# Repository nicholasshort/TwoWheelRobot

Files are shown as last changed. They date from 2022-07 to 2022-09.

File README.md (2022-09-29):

# TwoWheelRobot

This is a project I started to learn more about control theory. 

The project consists of three main folders:
1) Arduino Code
2) Hand Derivations for the Linearized State Space Model of a Pendulum on a Cart
3) Matlab/Python Pendulum on a Cart Simulation Files

I will try to go over each folder in the remainder of this readme.

# The Robot

The Bill of Materials for this project can be found here: https://docs.google.com/document/d/1V8id3cu9YUFI_mSXT52ZumMh5tL_UX_wbOAgka5fCik/edit?usp=sharing

To control the robot, I use a PID controller, with the help of a Kalman filter (defined in KalmanFilter.h) to filter out the noise from the accelerometer and to factor in gyroscope drift. A good artilce on the fundamentals of the Kalman filter can be found here: https://blog.tkjelectronics.dk/2012/09/a-practical-approach-to-kalman-filter-and-how-to-implement-it/

One thing to note for my design was that the position of the IMU board relative to the base of the robot resulted in greater angular accelerations and thus greater noise from the accelerometer. Therefore, the measurement noise variance had to be set to a greater value than the generic value recommended in the article above. 

Here is a video of the robot maintaining balance on youtube: 

Robot (https://www.youtube.com/shorts/AJx97sAAVso)

# Hand Derivations

The two wheel robot can be modeled as a pendulum on a cart. I used Newton's Laws to derive the state space model of the pendulum-cart system, and then reduced the number of states to only focus on the angle of the pendulum.

# Matlab and Python Simulations

I used matlab and python to simulate/verify my the state space model from my hand derivations, and to develop a full-state feedback control loop to control the cart and pendulum about a fixed angle and position respectively. Running PendulumCartSim.py will show a small animation of the implementation of this control law.

Here is the animation without any control:
final_631eb3e16659cb00835e07b7_296242

Here is the animation of the linearized system with full state feedback:
final_631eb2a96fb6b5005e3506c4_549431

Additionally, I also tried to control the system using a PID controller. In "PID_Tuning.m", I implemented a very slow root-locus plot in Matlab to generate proper PID gain values to stabilize the system. An example of the root locus plot can be seen below.

Root Locus

I then used the PID values found from the locus plot to plot the system's step response (Note these are not optimal PID values)

Step Response

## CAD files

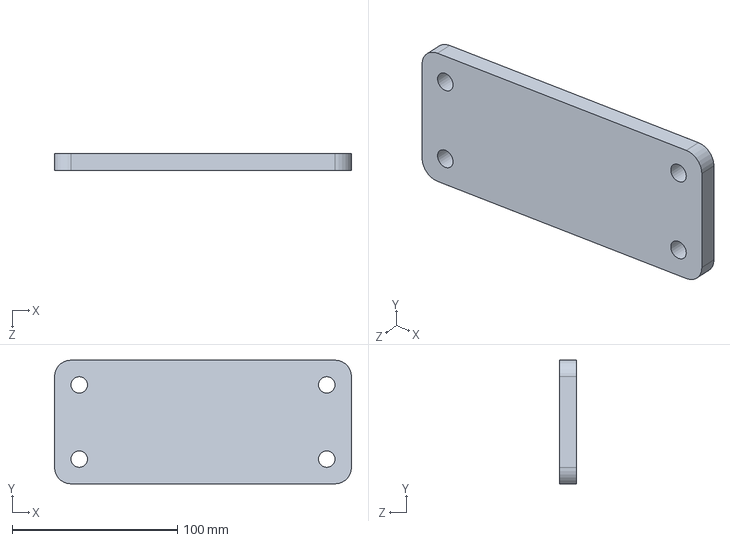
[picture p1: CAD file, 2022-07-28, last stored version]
Assembly/Platform.SLDPRT
180.0 x 75.0 x 10.0 mm

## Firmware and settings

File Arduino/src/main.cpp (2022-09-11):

#include <Arduino.h>
#include <Wire.h>
#include "KalmanFilter.h"
#include "MPU6050_Sensor.h"

#define PWM_A 6
#define PWM_B 5
#define IN_1 9
#define IN_2 7
#define IN_3 13
#define IN_4 12


MPU6050_Sensor mpu;

// Variances
float Qo = 0.001;
float Qb = 0.003;
float R = 20;

KalmanFilter kalmanFilter(Qo, Qb, R);

// Timers
unsigned long timer = 0;
float timeStep = 0.01;

// State
float* state = (float*)calloc(2, sizeof(float));

// Error variables
float error = 0;
float prevError = 0;
float totalError = 0;

// Angle
float desiredAngle = 0;

// PID Values
float Kp = 500;
float Ki = 15;
float Kd = 700;

// Controller Output
float output = 0;

// Start state variable
bool start = false;

void setup() 
{
  Serial.begin(115200);

  Serial.println("Starting...");

  state[0] = -85;

  mpu.begin();

  // Initialize pinout
  pinMode(PWM_A, OUTPUT);
  pinMode(PWM_B, OUTPUT);
  pinMode(IN_1, OUTPUT);
  pinMode(IN_2, OUTPUT);
  pinMode(IN_3, OUTPUT);
  pinMode(IN_4, OUTPUT);

}

void loop()
{
  timer = millis();

  // Read accelerometer values
  float accelX = mpu.getAccelXAxis();
  float accelY = mpu.getAccelYAxis();
  float accelZ = mpu.getAccelZAxis();

  // Read gyro value
  float gyroY = mpu.getGyroYAxis();

  // Calculate Pitch
  float pitch = -atan(accelX / sqrt(accelY * accelY + accelZ * accelZ)) * RAD_TO_DEG;

  // Run measurement through kalman filter
  state = kalmanFilter.update(state, pitch, gyroY, timeStep);

  // Error calculations
  error = state[0] - desiredAngle;

  if(abs(error) > 45) start = false;

  if(abs(error) < 1) start = true;

  if(start){ 

    // Integral error
    totalError = totalError + error;

    // Constrain total error
    if(totalError > 500) totalError = 500;
    if(totalError < -500) totalError = -500;
 
    // PID Calculations
    output = Kp*error + Ki*totalError + Kd*(error - prevError);
    output = map(abs(output), 0, 1250, 0, 255);
    output = output > 255 ? 255 : output;

  }

  output = start ? output : 0;
  Serial.println(state[0]);
  prevError = error;
  
  if(error < 0) {
    digitalWrite(IN_1, LOW);
    digitalWrite(IN_2, HIGH);
    digitalWrite(IN_3, LOW);
    digitalWrite(IN_4, HIGH);
    analogWrite(PWM_A, output);
    analogWrite(PWM_B, output);
  }else{
    digitalWrite(IN_1, HIGH);
    digitalWrite(IN_2, LOW);
    digitalWrite(IN_3, HIGH);
    digitalWrite(IN_4, LOW);
    analogWrite(PWM_A, output);
    analogWrite(PWM_B, output);
  }

  // Wait to full timeStep period
  delay((timeStep*1000) - (millis() - timer));

}

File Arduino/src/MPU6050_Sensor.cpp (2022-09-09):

#include "MPU6050_Sensor.h"

uint8_t MPU6050_Sensor::board_address_read = 0x68;
uint8_t MPU6050_Sensor::power_mgmt_1 = 0x6B;
uint8_t MPU6050_Sensor::gyro_config = 0x1B;
uint8_t MPU6050_Sensor::gyro_xout_h = 0x43;
uint8_t MPU6050_Sensor::gyro_yout_h = 0x45;
uint8_t MPU6050_Sensor::accel_xout_h = 0x3B;
uint8_t MPU6050_Sensor::accel_yout_h = 0x3D;
uint8_t MPU6050_Sensor::accel_zout_h = 0x3F;

void MPU6050_Sensor::begin() {
    Wire.begin();
    Wire.beginTransmission(board_address_read);
    Wire.write(power_mgmt_1); 
    Wire.write(0x08); // Turn off temperature sensor
    Wire.endTransmission(true);
    delay(50);
    Wire.beginTransmission(board_address_read);
    Wire.write(gyro_config);
    Wire.write(0x00); // Configure Gyroscope FS_SEL bits
    Wire.endTransmission(true);
}

float MPU6050_Sensor::getGyroXAxis() {
    Wire.beginTransmission(board_address_read);
    Wire.write(gyro_xout_h);
    Wire.endTransmission(true);
    Wire.requestFrom(board_address_read, 2, true);
    int16_t gyroXRaw = Wire.read() << 8 | Wire.read();
    return gyroXRaw / 131.0f; // Remove LSB unit
}

float MPU6050_Sensor::getGyroYAxis() {
    Wire.beginTransmission(board_address_read);
    Wire.write(gyro_yout_h);
    Wire.endTransmission(true);
    Wire.requestFrom(board_address_read, 2, true);
    int16_t gyroYRaw = Wire.read() << 8 | Wire.read();
    return gyroYRaw / 131.0f; // Remove LSB unit
}

float MPU6050_Sensor::getAccelXAxis() {
    Wire.beginTransmission(board_address_read);
    Wire.write(accel_xout_h);
    Wire.endTransmission(true);
    Wire.requestFrom(board_address_read, 2, true);
    int16_t accelXRaw = Wire.read() << 8 | Wire.read();
    return accelXRaw / 16384.0f; // Remove LSB unit
}


float MPU6050_Sensor::getAccelYAxis() {
    Wire.beginTransmission(board_address_read);
    Wire.write(accel_yout_h);
    Wire.endTransmission(true);
    Wire.requestFrom(board_address_read, 2, true);
    int16_t accelYRaw = Wire.read() << 8 | Wire.read();
    return accelYRaw / 16384.0f; // Remove LSB unit
}

float MPU6050_Sensor::getAccelZAxis() {
    Wire.beginTransmission(board_address_read);
    Wire.write(accel_zout_h);
    Wire.endTransmission(true);
    Wire.requestFrom(board_address_read, 2, true);
    int16_t accelZRaw = Wire.read() << 8 | Wire.read();
    return accelZRaw / 16384.0f; // Remove LSB unit
}

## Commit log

2022-07-28 Added platform part
    [Platform.SLDPRT]
2022-08-06 Added some simulation files and PID tuning scripts
    [Platform.SLDPRT]
2022-08-09 Created arduino project files
2022-08-28 Added PID controller to code
2022-09-02 Added code for Kalman Filter
2022-09-02 Added Kalman filter to robot code
2022-09-09 Added ability to read accelerometer values and calculate pitch. Kalman filter works well now!
2022-09-11 Finished tuning Kalman and PID values
2022-09-11 Removed assembly directory
    [Platform.SLDPRT]
